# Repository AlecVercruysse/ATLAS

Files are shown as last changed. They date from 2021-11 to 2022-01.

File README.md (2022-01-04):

# ATLAS: Audio Tracking Laser-Assisted Light Show

Arya Goutam and Alec Vercruysse

---

This work, completed as a final project for E155 at Harvey Mudd College, takes in music input via a 3.5mm audio jack, and syncs
a diffraction-grating based laser light show to respond to percussive elements in the song. Read our [final report](papers/report.pdf) for a description of 
the design and algorithm.

Due to the requirements of the project for the class, all SystemVerilog code, including that for the FFT, was written from scratch.

 - `fpga/` contains the SystemVerilog code used to interface with the PCM1808 ADC, the FFT module, and the beat tracking algorithm. It also includes the python files used to generate the twiddle and hann windowing look up tables.
 - `mcu/` contains the code for the microcontroller, which was responsible for selecting patterns, driving the servo, and controlling the relays.
 - `adc/` contains the design files for the PCB developed to interface the ADC with the development platform we used for the class
 - `papers/` contains the initial project proposal and final report
 - `sim/` contains the jupyter notebooks used to prototype different parts of the design.

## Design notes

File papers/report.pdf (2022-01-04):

E155 MICROPROCESSORS. FINAL PROJECT. DECEMBER 2021 | 1

# ATLAS: Audio Tracking Laser-Assisted Light Show

## Arya Goutam and Alec Vercruysse

CONTENTS

I | Introduction | 1
I-A | Motivation | | 1
I-B | Overview | | 1
II | Design | 1
II-A | FPGA Design | | 1
II-A1 | ADC Interface | | 2
II-A2 | Fast | Fourier | Transform
Computation | | 3
II-A3 | Beat Onset Detection . . . . | 3
II-B | Microcontroller Design | | 4
III | Results | 5
Appendix A: Bill of Materials | 6
Appendix B: MAX10 FPGA SystemVerilog Code | 7
B-A | i2s.sv | | 7
B-B | fft.sv | | 12
B-C | spi.sv | | 18
B-D | beat_track.sv | | 21
B-E | testbenches.sv | | 23
B-F | twiddle.py | | 29
B-G | fft.cpp | | 30
Appendix C: STM32F401RE C Code | 33
C-A | Servo.c | | 33
References | 37

Abstract—We propose a design of a system that projects a laser light show that synchronizes to to music. The system samples audio input with a PCM1808 stereo ADC, and a MAX10 FPGA analyzes the frequency content of the song to find percussive elements in order to determine beat onsets. An STM32 microcontroller uses the beat onset locations to control a servo that rotates a multi-pattern diffraction grating and two laser diodes which shine through this grating. While in practice the design requires the song to have percussive elements and the algorithm is sensitive to input audio volume, the system can accurately identify and rapidly responds to beats and produces a compelling visual effect.

I. INTRODUCTION
A. Motivation

### Light shows are often used to enhance music but coordi-

nating lighting with music is challenging to do on the fly,

### especially with a low-cost setup. Our goal for this project

A. Goutam and A. Vercruysse are Engineering Majors in the class of 2023 at Harvey Mudd College, CA.

### was to design a system that automatically creates interesting

lighting effects which are synchronized to a live audio input.

B. Overview

### The system shown in Figure 1 above is described here:

1) Stereo audio is passed from a computer to the PCM.
2) The PCM passes digital audio output to the FPGA.

### 3) The FPGA reads the digital audio, computes beat onsets and sends pulses to the MCU when it detects a beat

onset.

### 4) The MCU uses the beat onset pulses to compute the song’s tempo, choose a light pattern according to the tempo, and synchronize the pattern with the beats of the

song.

### 5) The synchronized light pattern is displayed via control

signals to the lasers and the servo.

II. DESIGN

### The system consists of a straightforward signal path that

starts as the PCM1808 ADC samples the stereo audio input,

### and is then processed by the MAX10 FPGA. The FPGA then outputs beat onset information to the STM32 MCU, which

drives a hobby servo motor with diffraction grating attached.

A. FPGA Design

### The 10M08SAU169 FPGA is responsible for interfacing with the PCM1808 stereo audio ADC as well as performing the digital signal processing required to determine beat onsets from the audio signal. Beat detection is performed based on

the threshold detection of a spectral-based novelty function.

TABLE I
10M08SAU169 FPGA RESOURCE USAGE
Total Logic Elements | 6,060 / 8,064 | 75%
Total Pins | 26 / 130 | 20%
Total Memory Bits | 1,024 / 387,072 | < 1%
Total 9-bit multipliers | 12 / 48 | 25%

### This FPGA had just enough logic elements to implement all modules, including I2S, FFT, and beat detection. Table I demonstrates that 75% of logic elements are being used by the current design. However, since memory usage is extremely

small (corresponding to a single 32 bit x 32 sample RAM),

### Quartus is preferring to infer register logic rather than memory for some memory modules including twiddle bit ROM and

FFT RAM.

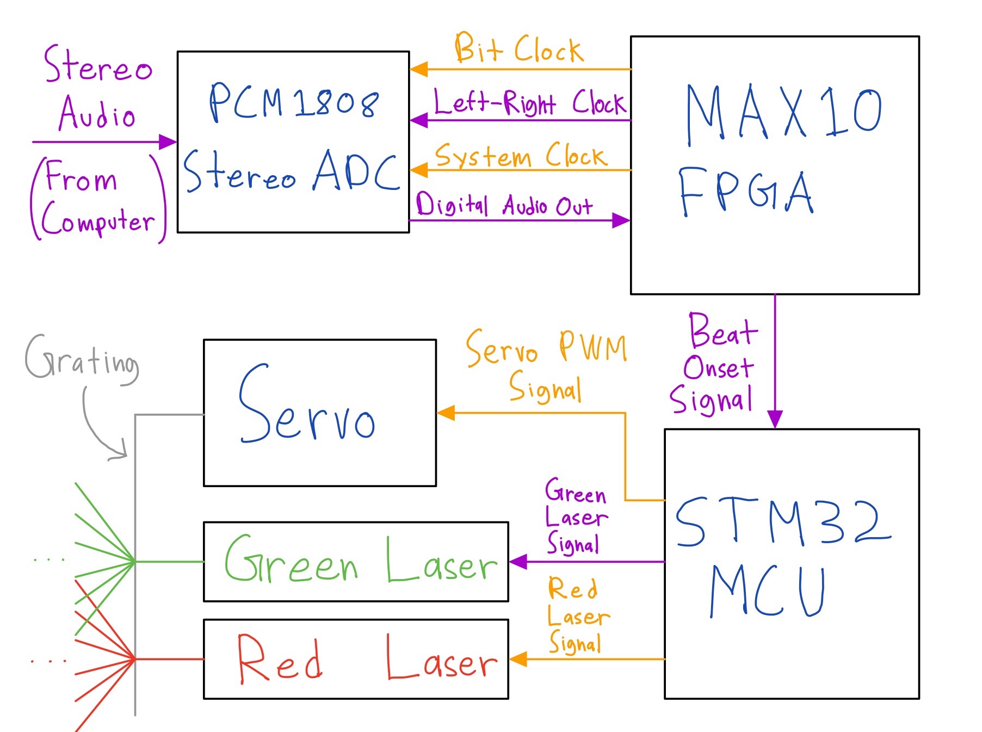
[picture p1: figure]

Fig. 1. System Block diagram displaying all components and signal paths within system.

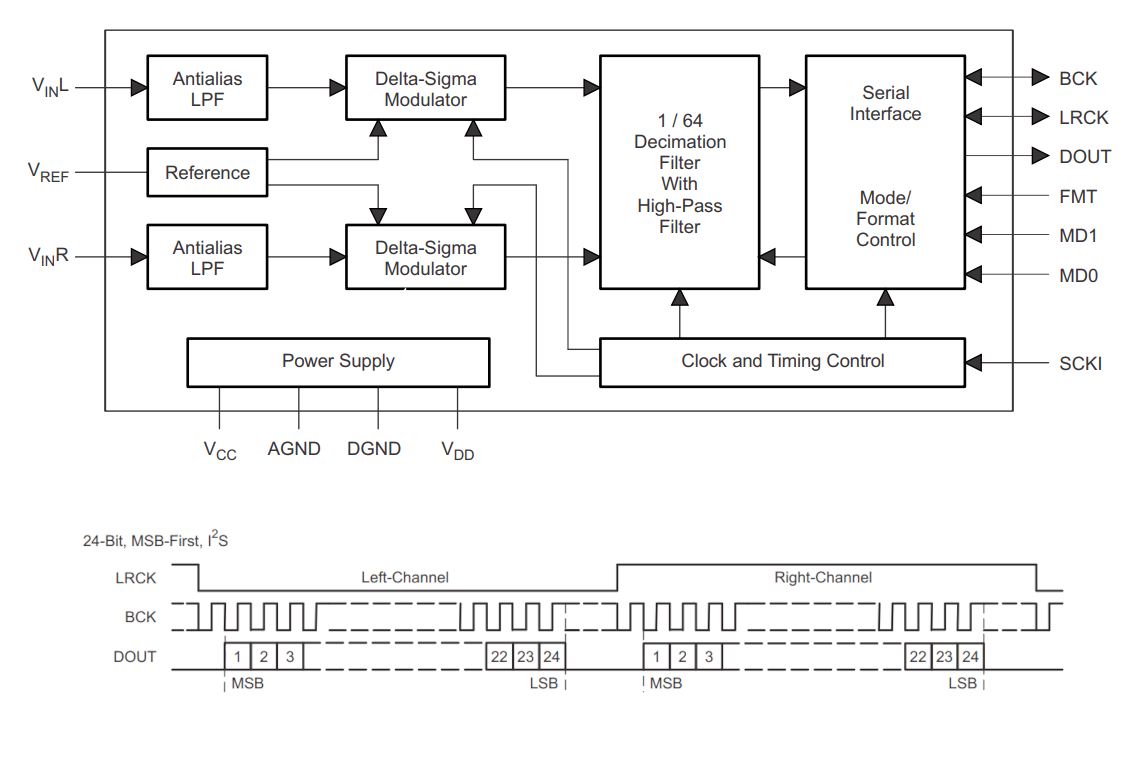
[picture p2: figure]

Fig. 2. Block diagram and relevant I2S communication protocol of the of the PCM1808 ADC used for audio input sampling. MD1=0, MD0=0, and FMT=0 to set the operating mode to slave-mode with I2S communication. AGND and DGND were tied together, with VCC and VDD tied to the 5V and 3.3V outputs of the Nucleo-64 development board, respectively.

### 1) ADC Interface: Although the FPGA includes an on-

board ADC, an external one was used to sample the audio.

### This was done in order to reduce the complexity of external hardware as well as provide for maximum possible flexibility

and minimum possible noise.

### Since conventional line-level audio signals are stereo, two

ADC channels are required in order to sample the song.

### Furthermore, line-level audio is zero centered, while the FPGA can only work with positive voltage, so therefore the signal would require biasing to sample with an FPGA. Lastly, the PCM1808 is much higher-performance than the FPGA – not only does it have 24 bit resolution (versus 12), it also

performs all required anti-aliasing filtering before sampling.

For a nominal 44.875 kHz sample rate, the PCM1808 samples at 3 MSPS and performs decimation and high pass to ensure that no aliasing occurs and no DC component exists in the signal. In addition, the PCM1808 exposes an extremely simple I2S slave-mode interface that allows for a fully synchronous design with the FPGA driving all sampling clocks, to allow for simple integration with the rest of the system. Lastly, the device requires only 3.3V and 5V power supplies, both of which already exist on the MAX10/Nucleo-64 development platform that is used for all work in E155. The block diagram

and I2S communication example waveform can be seen in Fig.

2.

Since the purpose of the E155 final project focused on digital logic design and no points were given for analog front end (AFE) design, the flexibility of the simple all-in-one solution of the PCM1808 was preferred to a more custom AFE that leveraged the existing ADC on-board the FPGA. The low component count required of this design also allowed for the extremely quick single-iteration development of a PCB for the PCM1808 and all associated audio jacks required to interface

the system with input audio.

A custom PCB was developed that included input (and output) 3.5mm and RCA audio jacks that allow the system to sit as a "man-in-the-middle" between an audio source and amplifier or listening device. The schematic of the PCB can be seen in Fig. 3. For maximum flexibility, all control signals were routed to the FPGA. Ultimately, the slave-mode I2S interface was selected, sampling at 46.875 kHz. This sampling frequency allows for a Nyquist frequency above 20 kHz, which

is considered to be the upper frequency limit of human hearing.

### Therefore this sampling frequency should accurately capture all audible information in the analog audio input. Since the

FPGA runs at 12MHz, the PCM1808 system clock (scki),

### which runs at 256∗46.875KHz = 12MHz was derived directly from the FPGA. Furthermore, a power of 2-based prescaler was used to derive the associated left/right clock (lrck) and

bit clock (bck) signals required for I2S communication.

### Since all I2S clock signals were derived from the same prescale counter, the value of the counter was also used to

determine state for the I2S master input module on the FPGA.

### For example, the bit index was determined by sampling the 5 bits (6:2) above the bit index sampled to derive the bit clock

(1).

### The bit index and left-right select clock were used to determine when to shift input data into the left and right channel shift registers. At the end of each frame consisting of a left and right channel sample, stable left/right sample registers were written to and an output "sample ready"

(newsample_valid) signal was generated.

### The operation of the I2S input module was verified via a

unit-testbench in ModelSim.
2) Fast Fourier Transform Computation: The 32-point Fast

Fourier Transform (FFT) is computed using a multi-cycle module based on the non-pipelined reference implementation by Slade in [1]. The design consists of a single butterfly unit which reads from and writes to two dual-port RAM blocks "ping-pong" configuration. That is, for a certain level of FFT computation, one RAM is reading pairs of a and b inputs to

the butterfly while the other is writing the resultant values. On the next level, the reading RAM becomes the writing one,

and the writing RAM becomes the reading one. An address generation unit (AGU) controls the logic to handle both the ping-pong operation of the RAM as well as determine the pairs of values that need to serve as inputs to the butterfly operation at each clock cycle. A block diagram of this implementation

is shown in Figure 4.

### Additional control logic was implemented in order to load the RAM with samples prior to computation, read the output

### spectrum values after computation, and reset the module after

computation.

### The state of the FPGA was determined by an external control Finite State Machine composed of the states

FFT_LOADING, FFT_STARTING, FFT_WAITING, FFT_WRITING and FFT_RESETTING. The state machine

waits in the FFT_LOADING state until 32 samples are loaded into the FFT, at which point it enters the FFT_STARTING state to drive the start logic. The state machine then enters the FFT_WAITING logic until it receives the done signal from the AGU. At this point the state machine enters the FFT_WRITING state to allow the output spectrum values to be read into another module. This control module also generates the addresses required to properly load and write out the data into and out of the FFT module. Once all values are written, the state machine enters FFT_RESETTING to reset the AGU before the next computation. After this, the

state goes back to FFT_LOADING and the cycle is repeated.

### The load logic was implemented by inferring multiplexers

between the AGU and RAM0 that allowed the write-enable,

### write-data, and address lines to be controlled by a load module that takes the input samples and writes them in the correct order to the FFT RAM 1

### The write logic was implemented in a similar manner, by inferring multiplexers that allowed the external FFT control module to access the address port of the RAM containing the

output values.

### The FFT computation is computed in less time than it takes to receive a single sample from the ADC, so all samples read in by the ADC are ultimately fed into the FFT module. This essentially results in an STFT module with a hop size equal

to the window size of 32.

The FFT module was verified with a unit-testbench in ModelSim, specifically by comparing output spectra to ones computed on identical input in Python with NumPy. Note that the output values reported in Table V of Slade do not match the values reported in Figure 3 of Slade, and are incorrect. Furthermore, our implementation uses roots-of-unity (twiddle) values wm = e

### −j2πm/N , while Slade uses a less standard convention, wm = e

### j2πm/N , which means that the sign of the imaginary parts of the output values produced

by the two different implementations of the FFT are flipped.

A crucial resource used when testing the FFT module was referencing a working C implementation (adapted from the one in Slade), which allowed ground-truth intermediate values to be examined. This was crucial to verifying the operation of the butterfly unit and address generation unit in particular. The

reference implementation is included in Appendix B-G.

### 3) Beat Onset Detection: The spectrum of a song can be considered to contain both harmonic and percussive information. Harmonic instruments and voices typically produce fundamental tones below 1 kHz, with harmonics of lower intensity appearing in frequency bins that are multiples of the

fundamental. Percussive elements, however, such as drums, can be considered to generate impulses in the time domain.

### Impulses in the time domain correspond to spectral content at

1with bit reversed addresses, see [1]

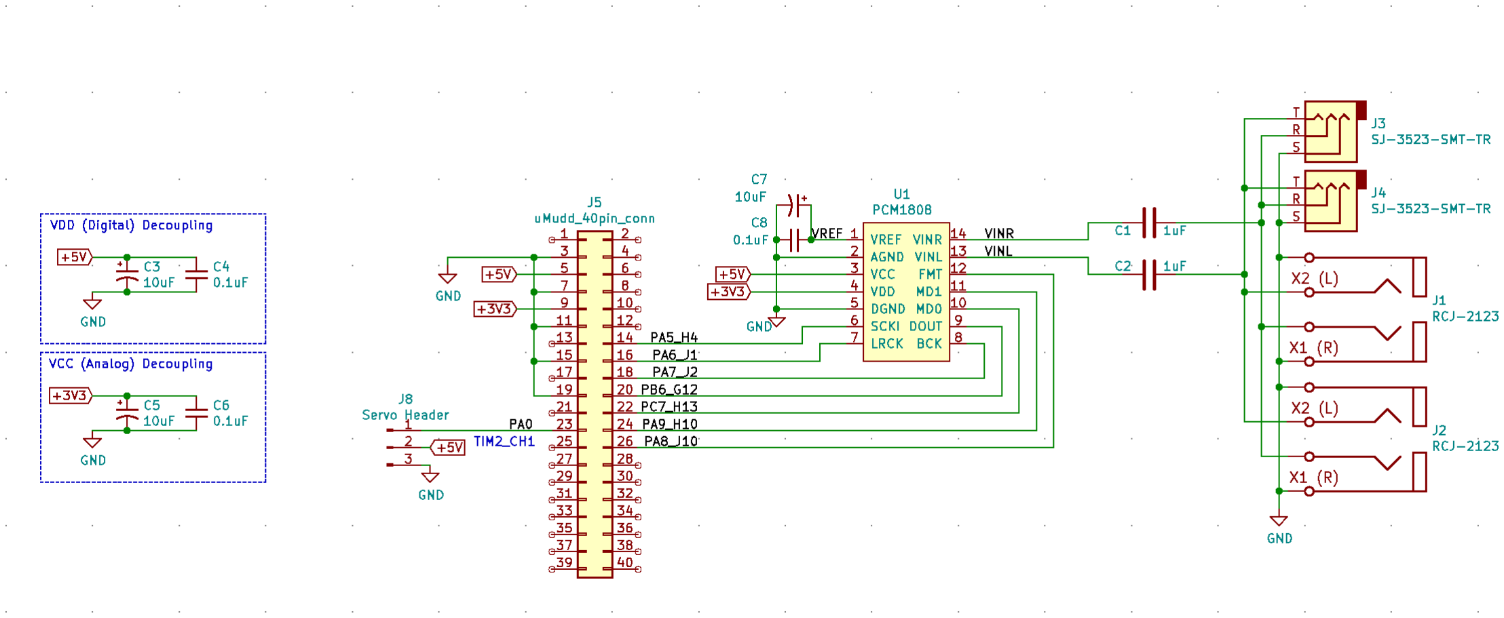
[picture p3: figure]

Fig. 3. Schematic of the ADC interface PCB. Note that the multiple audio jacks that allow it to be placed in the middle of an existing audio system.

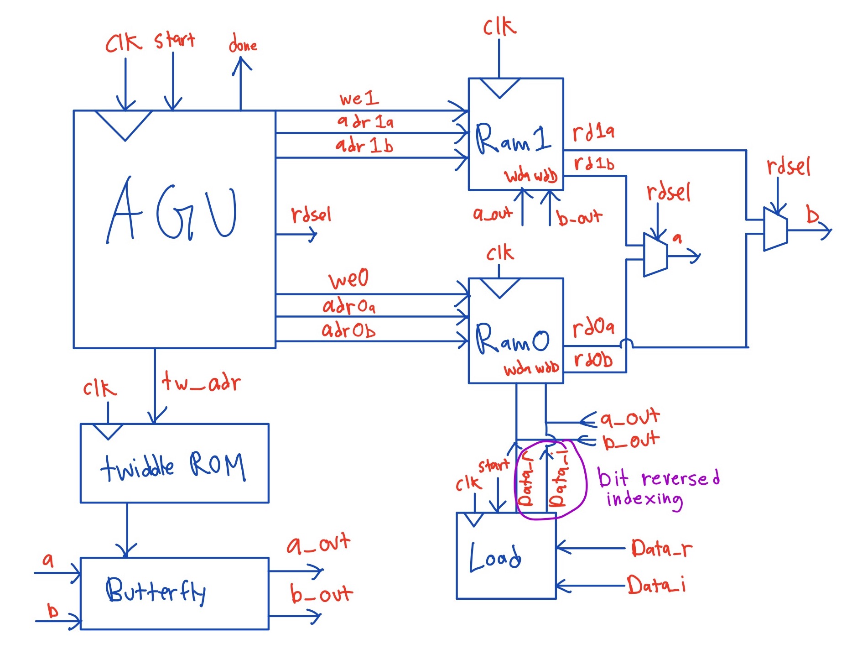
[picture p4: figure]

Fig. 4. Diagram of our Cooley-Tukey FFT System Verilog implementation based on Slade’s paper and Prof. Brake’s slides [1].

### every frequency, so often drums and percussive elements will appear in high-frequency bins, depending on the mastering of the song and the specific instruments involved. Figure 5 displays an example spectrum of an electronic dance music

(EDM) song that demonstrates this.

### To take advantage of the high-frequency and broadband nature of percussive components, beat onsets were calculated by performing debounced thresholding of a novelty function computed by summing the magnitudes of the upper frequency

bins.

As the output values of the FFT are being read sequen-tially, a complex multiplier computes the magnitude of each frequency bin by multiplying it with its complex conjugate. If the bin is between bins 10 and 15 inclusive, an accumulator accumulates this magnitude. The value of the accumulator is compared to a threshold to determine whether or not the sample could correspond to a beat. Hysteresis is implemented

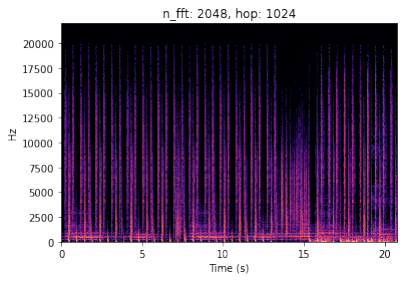
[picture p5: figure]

Fig. 5. Example log-magnitude Spectrum of a snippet of the EDM song "ACRAZE - Do it to It". Note that the upper frequency bins that correspond to the hi-hats provide steady tempo information, while the melodic and vocal parts of the song rest primarily in the lower frequency bins.

### to ensure that a single beat in the song that spans multiple

samples does not trigger the beat onset detector multiple times.

### Fig. 6 demonstrates this hysteresis for an example beat in a

song.

B. Microcontroller Design

### The STM32F401RE microcontroller (MCU) reads a pulsed beat onset signal from the FPGA and creates light patterns by

controlling the servo and the two lasers.

### The servo position is controlled by changing the duty cycle of a square wave signal. 770 µs of high time out of 20 ms corresponds to a position of zero degrees while 2270 µs corresponds to a position of 180 degrees. Positions are referred to as x µs. Our MCU simply writes out two binary signals for

laser control.
The lasers are controlled with a dual laser driver circuit.

### To create this circuit, we used a prebuilt dual laser driver

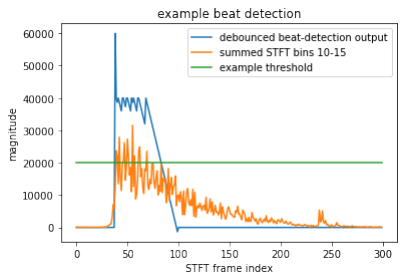
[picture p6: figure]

Fig. 6. Example beat-detection in the EDM song "ACRAZE - Do it to It". The orange trace corresponds to the sum of the upper frequency bins. The blue trace (beat detection out) goes high when the threshold is first reached. A "debounce" timer then counts down from there, resetting every time the threshold is reached, to only allow the beat to be detected again once the orange trace has been below the threshold for some minimum time. In practice, the blue signal only goes high when the beat is first detected, and the counter logic is stored and handled separately, but the logic displayed in this figure is helpful for visualization of the algorithm.

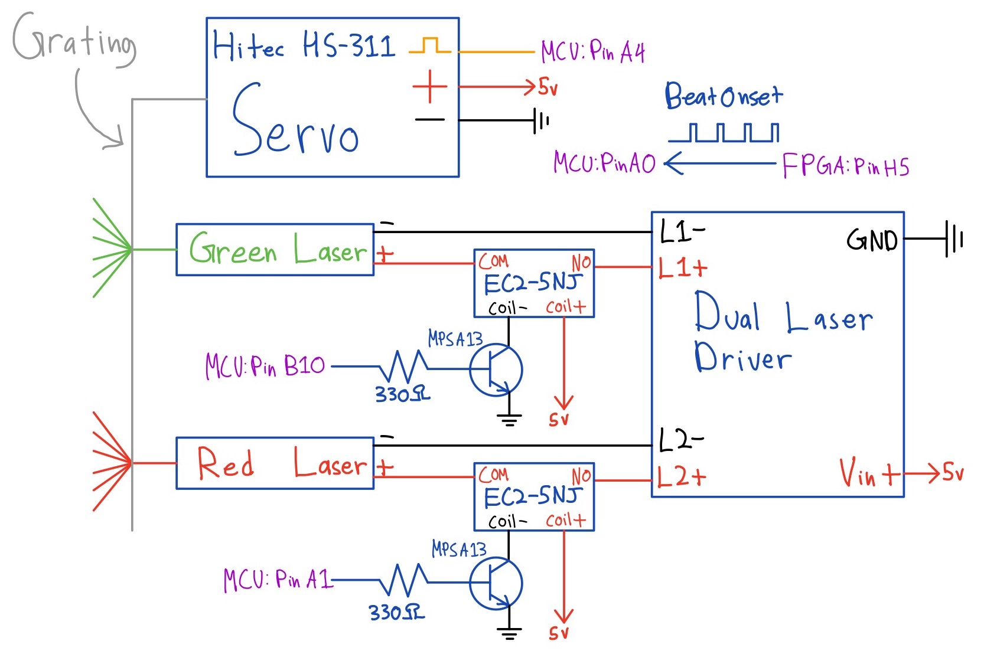
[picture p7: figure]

Fig. 7. Circuit diagram detailing physical connections between MCU, servo, and lasers.

board and inserted relays into the power wires going to the lasers. The MCU digital pins could not source enough current to activate the relays so we used NPN transistors to drive the relays and electrically control the flow of power to the lasers. We chose to use a relay instead of a transistor to avoid modifying the properties of the existing laser driver circuit. A circuit diagram of our MCU subsystem is presented in Figure

7.

A light pattern is encoded with four values: 1) Servo Starting Rotation (pulse width µs) 2) Servo Ending Rotation (pulse width µs) 3) Red Laser On (0 or 1) 4) Green Laser On (0 or 1) Beats per minute (BPM) is calculated using the time dif-ference between the last two beat onset pulses, and a pattern is assigned depending upon which bucket the BPM falls into from the following:

### - 0 < BPM ≤ 30 - 30 < BPM ≤ 60 - 60 < BPM ≤ 120 - 120 < BPM ≤ 240

### Once a pattern is selected, the servo oscillates between the servo start position and the servo end position. These transitions happen exactly at the beat onset times. The MCU also enables the lasers according to the selected pattern by writing the two binary "laser on" signals to our laser driver

circuit.

III. RESULTS

### The efficacy of our system is highly dependent upon the song that is fed into it. Songs with a consistent percussive

element, such as a clap or drum hit, produced the best results.

### In these cases, the beat onset detection algorithm captures nearly all of the beats and the lasers produce an aesthetically interesting light show that is closely synchronized to the input song. Additionally, the system functions best when the input

song is sent at maximum volume.

### There are a few ways we could have improved the system given more time: 1) Introduce an automatic gain control circuit. We believe this would allow for songs at varying volumes to perform

well with ATLAS.

### 2) Compute a log-magnitude spectrogram. Humans per-ceive the loudness of sound on a log scale so operating on a log-magnitude spectrogram is likely to yield beat detections that better align with a human’s perception of

beats.

### 3) Reduce the hop size of the STFT to be half of the window size by double-buffering the input sample win-dows, which provides for a more conventional STFT

computation.

4) Experiment with different FFT window sizes and bucket summation indices. Varying the window size and bucket summation indices could allow ATLAS to work on a greater variety of musical genres. For example, a higher FFT window size with beat detection based on a summation of the low frequency buckets could produce good

beat tracking in rock songs with a prominent bassline.

### Higher frequency resolution that enables the spectrum to differentiate fundamental frequencies of different notes would also enable the system to operate successfully with more conventional beat-detection algorithms such

as spectral-flux based novelty functions.

ACKNOWLEDGMENT

### The authors would like to thank Prof. Joshua Brake for his invaluable guidance with our final project. We also appreciate

the insightful feedback we received on our project by the class.

### Lastly, we thank Sam Abdelmuati in the stockroom for his help

regarding part selection.

APPENDIX A
BILL OF MATERIALS

TABLE II
BILL OF MATERIALS
Ct. | Description | Part Number | Extended Price
1 | stereo ADC | PCM1808PW | $2.23
2 | cap cer 1uf 50v 0805 | C2012JB1H105K085AB | $0.374
3 | cap cer 0.1uf 50v 0805 | CGA4J2X8R1H104K125AA | $0.396
3 | cap cer 10uf 25v 0805 | C2012JB1E106M085AC | $1.26
2 | conn jack stereo 3.5mm SMD | SJ-3523-SMT-TR | $1.88
1 | conn header vert 40pos 2.54mm | SBH11-PBPC-D20-ST-BK | $0.73
5 | JLCPCB boards (+ shipping) | – | $8.98
1 | laser + diffraction grating module (https://www.ebay.com/itm/-/254626113887?mkevt=1&mkcid=16&mkrid=711-127632-2357-0) | ZQ-B338 | $20.99
1 | Hitec hobby servo | HS-311 | N/A 2
2 | relay | EC2-5NJ | N/A 3
2 | NPN darlington transistor | MPSA13 | N/A 4
2 | 330 ohm resistor | – | N/A 5

2
already owned
3
from stock room
4
from stock room
5
from stock room

APPENDIX B
MAX10 FPGA SYSTEMVERILOG CODE
A. i2s.sv
1 | module final_fpga(input logic | clk, | // | 12MHz MAX1000 clk, H6
2 | input logic | nreset, // | global reset, | E6 (right btn)
3 | input logic | din, // | I2S DOUT, | PB6_G12
4 | input logic | uscki, // | SPI clk, | PB3_J12
5 | input logic | umosi, // | SPI MOSI, | PB5_J13
6 | input logic | uce, // | SPI CE, | PA10_L12
7 | input logic [3:0] | sw1, // | threshold sel. | E1, C2, C1, D1
,→ | (DIP SW1)
8 | output logic | bck, // | I2S bit clock, | PA7_J2
9 | output logic | lrck, // | I2S l/r clk, | PA6_J1
10 | output logic | scki, // | PCM1808 sys clk, | PA5_H4
11 | output logic | fmt, // | PCM1808 FMT, | PA8_J10
12 | output logic [1:0] md, // | PCM1808 MD1 & MD0, PC7_H13, PA9_H10
13 | output logic | miso, // | SPI MISO, | PB4_K11
14 | output logic [7:0] LEDs, // | debug LEDs | (see MAX1000 user
,→ | guide)
15 | output logic | beat_out // beat (to MCU) | H5 (thru a jumper
,→ | to MCU)
16 | );

17
18 | ///////////////////////////////// reset
19 | // active high reset, active low btns
20 | logic | reset;
21 | assign reset = ~(nreset);
22 | //assign LEDs[0] = reset;
23 | ///////////////////////////////// end reset

24
25 | ///////////////////////////////// I2S/PCM1808
26 | assign md | = 2'b00; // see PCM1808 table 2 (slave mode)
27 | assign fmt = 0; | // see PCM1808 table 3 (i2s mode)

28
29 | logic | newsample;
30 | logic [23:0] | left, right;
31 | i2s pcm_in(clk, reset, din, bck, lrck, scki, left, right, newsample);
32 | ///////////////////////////////// end I2S/PCM1808

33
34 | ///////////////////////////////// FFT
35 | logic | fft_start, fft_done, i2s_load, fft_load,
,→ | fft_reset, fft_creset, fft_write;
36 | logic [31:0] | fft_wd;
37 | logic signed [15:0] | left_msbs;
38 | logic signed [15:0] | fft_rd;
39 | logic [5:0] | sample_ctr;

40
41 | assign fft_reset = reset | fft_creset;
42 | assign left_msbs = left[23:8];
43 | assign fft_rd | = left_msbs >>> 5; // arithmetic shift right
44 | fft fft(clk, fft_reset, fft_start, fft_load, fft_rd, fft_wd, fft_done);
45 | fft_control i2s_fft_glue(clk, reset, newsample, fft_done, fft_start, fft_load,
,→ | fft_creset, fft_write, sample_ctr);
46 | ///////////////////////////////// end FFT

47
48 | ///////////////////////////////// store result
49 | logic [31:0] | res_count; // result count

50 | logic | posedge_fft_done;
51 | pos_edge pos_edge_fft_done(clk, fft_done, posedge_fft_done);
52 | always_ff @(posedge clk)
53 | begin
54 | if | (reset) | res_count <= 0;
55 | else if (posedge_fft_done) res_count <= res_count + 1'b1;
56 | end

57
58 | logic [31:0] | | spectrum_result [0:31];
59 | always_ff @(posedge clk) begin
60 | if (fft_write)
61 | begin
62 | spectrum_result[sample_ctr] <= fft_wd;
63 | end
64 | end
65 | ///////////////////////////////// end store result

66
67 | ///////////////////////////////// SPI
68 | logic [31:0] spi_data;
69 | logic [4:0] | spi_adr;
70 | assign spi_data = spectrum_result[spi_adr];
71 | spi_slave spi(clk, reset, uscki, umosi, uce, spi_data, spi_adr, miso);
72 | ///////////////////////////////// end SPI

73
74 | ///////////////////////////////// beat tracking
75 | logic [7:0] | thresh, accum_stable;
76 | logic | beat_ctr, posedge_beat_out;
77 | assign thresh = {1'b0, sw1, 2'b0};
78 | assign LEDs | = {accum_stable[7:1], beat_ctr};
79 | beat_track beattrack(clk, reset, sample_ctr, fft_wd, fft_write, fft_done, thresh,
,→ | beat_out, accum_stable);
80 | pos_edge pos_edge_beat_out(clk, beat_out, posedge_beat_out);

81
82 | always_ff @(posedge clk) begin
83 | if (reset)
84 | beat_ctr <= 0;
85 | else if (posedge_beat_out)
86 | beat_ctr <= beat_ctr + 1'b1;
87 | end
88 | ///////////////////////////////// end beat tracking

89
90 endmodule // final_fpga

91
92 | typedef enum logic [3:0] {FFT_LOADING, FFT_STARTING, FFT_WAITING, FFT_WRITING,
,→ | FFT_RESETTING, FFT_ERROR} statetype;
93 | module fft_control(input logic | clk,
94 | input logic | reset,
95 | input logic | newsample,
96 | input logic | fft_done,
97 | output logic | fft_start,
98 | output logic | fft_load,
99 | output logic | fft_reset,
100 | output logic | fft_write,
101 | output logic [5:0] sample_ctr);

102
103 | statetype | | state, nextstate;

104
105 | always_ff @(posedge clk) begin

106 | if | (reset || (state == FFT_RESETTING))
107 | sample_ctr <= 0;
108 | else if ((newsample && (state == FFT_LOADING)) || (state == FFT_WRITING ||
,→ | nextstate == FFT_WRITING))
109 | sample_ctr <= sample_ctr + 1'b1;
110 | else if (state == FFT_WAITING)
111 | sample_ctr <= 0; // this case needs to be checked after the previous
112 | // | in case state is WAITING but nextstate is WRITING.
113 | end

114
115 | always_ff @(posedge clk) begin
116 | if (reset) state <= FFT_LOADING;
117 | else state <= nextstate;
118 | end

119
120 | always_comb begin
121 | case (state)
122 | FFT_LOADING | :
123 | if (sample_ctr == 32) | nextstate = FFT_STARTING;
124 | else | nextstate = FFT_LOADING;
125 | FFT_STARTING : | nextstate = FFT_WAITING;
126 | FFT_WAITING | :
127 | if (fft_done) | nextstate = FFT_WRITING;
128 | else | nextstate = FFT_WAITING;
129 | FFT_WRITING | :
130 | if (sample_ctr == 32) | nextstate = FFT_RESETTING;
131 | else | nextstate = FFT_WRITING;
132 | FFT_RESETTING: | nextstate = FFT_LOADING;
133 | default | : | nextstate = FFT_ERROR; // debug
134 | endcase // case (state)
135 | end

136
137 | assign fft_load | = (state == FFT_LOADING) & newsample;
138 | assign fft_start = (state == FFT_STARTING);
139 | assign fft_reset = (state == FFT_RESETTING);
140 | assign fft_write = (state == FFT_WRITING || nextstate == FFT_WRITING);

141
142 endmodule // control

143
144 | module i2s(input logic | clk,
145 | input logic | reset,
146 | input logic | din, // | PCM1808 DOUT, | PB6_G12
147 | output logic | bck, // | bit clock, | PA7_J2
148 | output logic | lrck, // left/right clk, | PA6_J1
149 | output logic | scki, // PCM1808 system clock, PA5_H4
150 | output logic [23:0] left,
151 | output logic [23:0] right,
152 | output logic | newsample_valid);

153
154 | /////////////////// clock ////////////////////////////////////

155
156 | // | Fs = 46.875 KHz
157 | logic [8:0] | prescaler; // 9-bit prescaler
158 | assign scki = clk; | // 256 * Fs = 12 MHz
159 | assign bck | = prescaler[1]; // 64 | * Fs = 3 MHz = 12 MHz / 4
160 | assign lrck = prescaler[7]; // 1 | * Fs = 12 Mhz / 256

161
162 | always_ff @(posedge clk)

163 | begin
164 | if (reset)
165 | prescaler <= 0;
166 | else
167 | prescaler <= prescaler + 9'd1;
168 | end
169 | /////////////////// end clock ////////////////////////////////

170
171 | // left and right shift registers
172 | logic [23:0] | lsreg, rsreg;

173
174 | // samples the prescaler to figure out what bit should currently be sampled.
175 | // sampling occurs on bit 1 and bit 24, NOT bit 0!
176 | logic [4:0] | bit_state;
177 | assign bit_state = prescaler[6:2];

178
179 | // shift register enable logic
180 | logic | shift_en;
181 | assign shift_en = ((bit_state >= 1) && (bit_state <= 24) && !reset);

182
183 | // shift register operation. samples DOUT only when shift_en.
184 | // this should be the only register that is not clocked directly from clk!!
185 | always_ff @(posedge bck)
186 | begin
187 | if (!lrck && shift_en) | // left
188 | begin
189 | lsreg <= {lsreg[22:0], din};
190 | rsreg <= rsreg;
191 | end
192 | else if (lrck && shift_en) // right
193 | begin
194 | rsreg <= {rsreg[22:0], din};
195 | lsreg <= lsreg;
196 | end
197 | end // shift register operation

198
199 | // load shift regs into output regs.
200 | // update both regs at once, once every fs.
201 | // this way, left and right will always contain a valid sample.
202 | logic newsample;
203 | assign newsample = (bit_state == 25 && lrck && prescaler[1:0] == 0); // once every
,→ | cycle
204 | assign newsample_valid = (bit_state == 26 && lrck && prescaler[1:0] == 0); // once
,→ | we can sample it!
205 | always_ff @(posedge clk)
206 | begin
207 | if (reset)
208 | begin
209 | left <= 0;
210 | right <= 0;
211 | end
212 | else if (newsample)
213 | begin
214 | left <= lsreg;
215 | right <= rsreg;
216 | end
217 | else
218 | begin

219 | left <= left;
220 | right <= right;
221 | end
222 | end

223
224 endmodule // i2s

B. fft.sv
1 | // the width is the bit width (e.g. if width=16, 16 real and 16 im bits).
2 | // the input should be width-5 to account for bit growth.
3 | module fft
4 | #(parameter width=16, N_2=5, hann=0) // N_2 is log base 2 of N (points)
5 | (input logic | clk,
6 | input logic | reset,
7 | input logic | start,
8 | input logic | load,
9 | input logic [width-1:0] | rd, // real | read data in
10 | output logic [2*width-1:0] wd, // complex write data out
11 | output logic | done);

12
13 | logic | enable; | // for AGU operation
14 | logic | rdsel; | // read from RAM0 or RAM1
15 | logic | we0_agu, we0, we1; // RAMx write enable
16 | logic [N_2 - 1:0] | adr0a_agu, adr0b_agu, adr0a, adr0b, adr0a_load,
,→ | adr0b_load, adr0a_load_agu, adr1a, adr1b, adr1a_agu;
17 | logic [N_2 - 2:0] | twiddleadr; // twiddle ROM adr
18 | logic [2*width-1:0] | twiddle, a, b, writea, writeb, aout, bout, rd0a, rd0b,
,→ | rd1a, rd1b, val_in;

19
20 | // LOAD LOGIC
21 | fft_load #(width, N_2, hann) loader(clk, reset, load, rd, adr0a_load, adr0b_load,
,→ | val_in);
22 | assign adr0a_load_agu = load ? adr0a_load : adr0a_agu;
23 | assign adr0b = load ? adr0b_load : adr0b_agu;
24 | assign writea = load ? val_in : aout;
25 | assign writeb = load ? val_in : bout;
26 | assign we0 | = load ? | 1'b1 : we0_agu;

27
28 | // AGU ENABLE LOGIC
29 | always_ff @(posedge clk)
30 | begin
31 | if | (start) enable <= 1;
32 | else if (done || reset) | enable <= 0;
33 | end

34
35 | // OUTPUT LOGIC
36 | logic [N_2-1:0] out_idx;
37 | assign wd | = N_2[0] ? rd1a : rd1b; // ram holding results depends on even-ness of
,→ | log2(N-points)s?
38 | assign adr0a = done ? out_idx : adr0a_load_agu;
39 | assign adr1a = done ? out_idx : adr1a_agu;

40
41 | always_ff @(posedge clk)
42 | begin
43 | if | (reset) out_idx <= 0;
44 | else if (done) | out_idx <= out_idx + 1'b1;
45 | end

46
47 | fft_agu #(width, N_2) agu(clk, enable, reset, done, rdsel, we0_agu, adr0a_agu,
,→ | adr0b_agu, we1, adr1a_agu, adr1b, twiddleadr);
48 | fft_twiddleROM #(width, N_2) twiddlerom(twiddleadr, twiddle);

49
50 | twoport_RAM #(width, N_2) ram0(clk, we0, adr0a, adr0b, writea, writeb, rd0a, rd0b);
51 | twoport_RAM #(width, N_2) ram1(clk, we1, adr1a, adr1b, | aout, | bout, rd1a, rd1b);

52 | assign a = rdsel ? rd1a : rd0a;
53 | assign b = rdsel ? rd1b : rd0b;

54
55 | fft_butterfly #(width) bgu(twiddle, a, b, aout, bout);

56
57 endmodule // fft

58
59 | module fft_load
60 | #(parameter width=16, N_2=5, hann=0) // hann: bool, whether or not to window.
61 | (input logic clk,
62 | input logic | reset,
63 | input logic | load,
64 | input logic [width-1:0] | rd,
65 | output logic [N_2-1:0] | adr0a_load,
66 | output logic [N_2-1:0] | adr0b_load,
67 | output logic [2*width-1:0] val_in);

68
69 | logic [N_2-1:0] | idx;
70 | logic [width-1:0] | val_in_re;

71
72 | bit_reverse #(N_2) reverseaddr(idx, adr0a_load);
73 | assign adr0b_load = adr0a_load;

74
75 | always_ff @(posedge clk)
76 | begin
77 | if (reset) begin
78 | idx <= 0;
79 | end else if (load) begin
80 | idx <= idx + 1'b1;
81 | end
82 | end

83
84 | logic | [2*width-1:0] untruncated_mult;
85 | logic signed [width-1:0] | hann_coeff;
86 | hann_lut #(width, N_2) hann_rom(clk, idx, hann_coeff);
87 | assign untruncated_mult = hann_coeff * rd;
88 | assign val_in_re = hann ? untruncated_mult[2*width-2:width-1] : rd;
89 | assign val_in | = {val_in_re, 16'b0}; // imaginary is all zeros!

90
91 endmodule // fft_load

92
93 | module bit_reverse
94 | #(parameter N_2=5)
95 | (input logic [N_2-1:0] in,
96 | output logic [N_2-1:0] out);

97
98 | genvar | i;
99 | generate
100 | for(i=0; i<N_2; i=i+1) begin : BIT_REVERSE
101 | assign out[i] = in[N_2-i-1];
102 | end
103 | endgenerate

104
105 endmodule // bit_reverse

106
107 | // 32-point FFT address generation unit
108 | module fft_agu
109 | #(parameter width=16, N_2=5)

110 | (input logic | | clk,
111 | input logic | | enable,
112 | input logic | | reset,
113 | output logic | | done,
114 | output logic | | rdsel,
115 | output logic | | we0,
116 | output logic [N_2-1:0] adr0a,
117 | output logic [N_2-1:0] adr0b,
118 | output logic | | we1,
119 | output logic [N_2-1:0] adr1a,
120 | output logic [N_2-1:0] adr1b,
121 | output logic [N_2-2:0] twiddleadr);

122
123 | logic [N_2-1:0] | fftLevel = 0;
124 | logic [N_2-1:0] | flyInd = 0;

125
126 | logic [N_2-1:0] | adrA;
127 | logic [N_2-1:0] | adrB;

128
129 | always_ff @(posedge clk) begin
130 | if (reset) begin
131 | fftLevel <= 0;
132 | flyInd <= 0;
133 | end
134 | // Increment fftLevel and flyInd
135 | else if(enable === 1 & ~done) begin
136 | if(flyInd < 2**(N_2 - 1) - 1) begin
137 | flyInd <= flyInd + 1'd1;
138 | end else begin
139 | flyInd <= 0;
140 | fftLevel <= fftLevel + 1'd1;
141 | end
142 | end
143 | end

144
145 | // sets done when we are finished with the fft
146 | assign done = (fftLevel == (N_2));
147 | calcAddr #(width, N_2) adrCalc(fftLevel, flyInd, adrA, adrB, twiddleadr);

148
149 | assign adr0a = adrA;
150 | assign adr1a = adrA;

151
152 | assign adr0b = adrB;
153 | assign adr1b = adrB;

154
155 | // flips every cycle
156 | assign we0 = fftLevel[0] & enable;
157 | assign we1 = ~fftLevel[0] & enable;

158
159 | // flips every cycle
160 | assign rdsel = fftLevel[0];

161
162 endmodule // fft_agu

163
164 | // todo: parameterize for more than 32-point FFT.
165 | module calcAddr
166 | #(parameter width=16, N_2=5)
167 | (input logic | [N_2-1:0] | fftLevel,

168 | input logic [N_2-1:0] | flyInd,
169 | output logic [N_2-1:0] adrA,
170 | output logic [N_2-1:0] adrB,
171 | output logic [N_2-2:0] twiddleadr);

172
173 | logic [N_2-1:0] | tempA;
174 | logic [N_2-1:0] | tempB;

175
176 | always_comb begin
177 | tempA = flyInd << 1'd1;
178 | tempB = tempA + | 1'd1;
179 | adrA = ((tempA << fftLevel) | (tempA >> (N_2 - fftLevel))) & 5'h1f;

180
181 | adrB = ((tempB << fftLevel) | (tempB >> (N_2 - fftLevel))) & 5'h1f;
182 | twiddleadr = ((32'hffff_fff0 >> fftLevel) & 32'hf) & flyInd;
183 | end
184 | endmodule // calcAddr

185
186 | module fft_twiddleROM
187 | #(parameter width=16, N_2=5)
188 | (input logic | [N_2-2:0] twiddleadr, // 0 - 1023 = 10 bits
189 | output logic [2*width-1:0] twiddle);

190
191 | // twiddle table pseudocode: w[k] = w[k-1] * w,
192 | // where w[0] = 1 and w = exp(-j 2pi/N)
193 | // for k=0... N/2-1

194
195 | logic [2*width-1:0] | vectors [0:2**(N_2-1)-1];
196 | initial $readmemb("rom/twiddle.vectors", vectors);
197 | assign twiddle = vectors[twiddleadr];

198
199 endmodule // fft_twiddleROM

200

201
202 | // make sure the script rom/hann.py has been run with
203 | // the desired width! the `width` param should be equal to `q` in the script.
204 | // todo: test hann windowing (does the read need to be clocked)?
205 | module hann_lut
206 | #(parameter width=16, N_2=5)
207 | (input logic | clk,
208 | input logic [N_2-1:0] | idx,
209 | output logic [width-1:0] out);

210
211 | logic [width-1:0] | vectors[2**N_2-1:0];
212 | initial $readmemb("rom/hann.vectors", vectors);

213
214 | always @(posedge clk)
215 | out <= vectors[idx];

216
217 endmodule // hann_lut

218

219
220 | // explicit so that it is inferred, and we control
221 | // the truncation of the output.
222 | module mult
223 | #(parameter width=16)
224 | (input logic signed [width-1:0] | a,
225 | input logic signed [width-1:0] | b,

226 | output logic signed [width-1:0] out);

227
228 | logic [2*width-1:0] | untruncated_out;

229
230 | assign untruncated_out = a * b;
231 | assign out = untruncated_out[30:15];
232 | // see slade paper. this works as long as we're not
233 | // multiplying two maximum mag. negative numbers.

234
235 endmodule // mult

236

237
238 | module complex_mult
239 | #(parameter width=16)
240 | (input logic [2*width-1:0] | a,
241 | input logic [2*width-1:0] | b,
242 | output logic [2*width-1:0] out);

243
244 | logic signed [width-1:0] | a_re, a_im, b_re, b_im, out_re, out_im;
245 | assign a_re = a[31:16]; assign a_im = a[15:0];
246 | assign b_re = b[31:16]; assign b_im = b[15:0];

247
248 | logic signed [width-1:0] | a_re_be_re, a_im_b_im, a_re_b_im, a_im_b_re;
249 | mult #(width) m1 (a_re, b_re, a_re_be_re);
250 | mult #(width) m2 (a_im, b_im, a_im_b_im);
251 | mult #(width) m3 (a_re, b_im, a_re_b_im);
252 | mult #(width) m4 (a_im, b_re, a_im_b_re);

253
254 | assign out_re = (a_re_be_re) - (a_im_b_im);
255 | assign out_im = (a_re_b_im) + (a_im_b_re);
256 | assign out = {out_re, out_im};
257 | endmodule // complex_mult

258
259 | module fft_butterfly
260 | #(parameter width=16)
261 | (input logic [2*width-1:0] twiddle,
262 | input logic [2*width-1:0] | a,
263 | input logic [2*width-1:0] | b,
264 | output logic [2*width-1:0] aout,
265 | output logic [2*width-1:0] bout);

266
267 | logic signed [width-1:0] | a_re, a_im, aout_re, aout_im, bout_re, bout_im;
268 | logic signed [width-1:0] | b_re_mult, b_im_mult;
269 | logic [2*width-1:0] | b_mult;

270

271
272 | // expand to re and im components
273 | assign a_re = a[2*width-1:width];
274 | assign a_im = a[width-1:0];

275
276 | // perform computation
277 | complex_mult #(width) twiddle_mult(b, twiddle, b_mult);
278 | assign b_re_mult = b_mult[31:16];
279 | assign b_im_mult = b_mult[15:0];

280
281 | assign aout_re = a_re + b_re_mult;
282 | assign aout_im = a_im + b_im_mult;

283

284 | assign bout_re

= a_re

- b_re_mult;
285 | assign bout_im

= a_im

- b_im_mult;

286
287 | // pack re and im outputs
288 | assign aout | = {aout_re, aout_im};
289 | assign bout | = {bout_re, bout_im};

290
291 endmodule // fft_butterfly

292

293
294 | // adapted from HDL example 5.7 in Harris TB
295 | module twoport_RAM
296 | #(parameter width
=16, N_2

=

5

)

297 | (input logic | clk,
298 | input logic | we,
299 | input logic [N_2

1

:

0] | adra,
300 | input logic [N_2

1

:

0] | adrb,
301 | input logic

[

2

*width

1

:

0] | wda,
302 | input logic

[

2

*width

1

:

0] | wdb,
303 | output logic

[

2

*width

1

:

| | 0] rda,
304 | output logic

[

2

*width

1

:

| | 0] rdb);

305

306 | reg [
| 2 *width

1

:

0] | mem [

2**N_2

1

:

0];

307
308 | always @(posedge clk)
309 | if (we)
310 | begin
311 | mem[adra] <= wda;
312 | mem[adrb] <= wdb;
313 | end

314
315 | assign rda = mem[adra];
316 | assign rdb = mem[adrb];

317
318 endmodule // twoport_RAM

319
320 | module complex_mag
321 | #(parameter width
=16

)

322 | (input logic

[

2

*width

1

:

0] | a,
323 | output logic

[

2

*width

1

:

| | 0] out);

324
325 | logic [
| 2 *width

1

:

0] | b;
326 | logic signed [width

1

:

0] | b_re, b_im;

327
328 | assign b_re

= a[31

:16];
329 | assign b_im

=

-a[15

:

0];
330 | assign b = {b_re, b_im};

331
332 | complex_mult mag_mult(a, b, out);

333
334 endmodule // magnitude

C. spi.sv
1 | typedef enum logic [3:0] {SPI_IDLE, SPI_LOAD, SPI_WAIT, SPI_SHIFT, SPI_ERROR}
,→ | spi_state;
2 | module spi_slave(input logic | clk,
3 | input logic | reset,
4 | input logic | uscki, // non-synchronus miso
5 | input logic | umosi, // non-synchronus mosi
6 | input logic | uce, | // non-synchronus chip-enable
7 | input logic [31:0] data, | // 32-bit. based on adr.
8 | output logic [4:0] adr, | // to address data ram
9 | output logic | miso);

10
11 | // cpol = 0 (idle low)
12 | // cpha = 1 (shift on leading edge (posedge), sample on lagging edge (negedge)
13 | logic | | | scki, mosi, ce;
14 | sync scki_sync(clk, uscki, scki);
15 | sync mosi_sync(clk, umosi, mosi);
16 | sync | ce_sync(clk, | uce, | ce);

17
18 | logic | | | posedge_scki;
19 | pos_edge pos_edge_scki(clk, scki, posedge_scki);

20
21 | logic [31:0] | data_out;
22 | logic [4:0] | bit_idx;
23 | spi_state state, nextstate;

24
25 | assign miso = data_out[31]; // MSB. shifted out

26
27 | // SPI state register
28 | always_ff @(posedge clk) begin
29 | if (reset) state <= SPI_IDLE;
30 | else state <= nextstate;
31 | end

32
33 | // SPI state transition logic
34 | always_comb begin
35 | case (state)
36 | SPI_IDLE : if (ce) nextstate <= SPI_LOAD;
37 | else | nextstate <= SPI_IDLE;
38 | SPI_LOAD : nextstate <= SPI_WAIT;
39 | SPI_WAIT : if (posedge_scki) begin
40 | if (bit_idx != 31) nextstate <= SPI_SHIFT;
41 | else nextstate <= SPI_LOAD;
42 | | end
43 | else if (~ce) nextstate <= SPI_IDLE;
44 | else | nextstate <= SPI_WAIT;
45 | SPI_SHIFT : nextstate <= SPI_WAIT;
46 | default : nextstate <= SPI_ERROR;
47 | endcase // case (state)
48 | end

49
50 | // adr logic
51 | always_ff @(posedge clk) begin
52 | if (state == SPI_IDLE)
53 | | adr <= 0;
54 | else if (state == SPI_LOAD)
55 | adr <= adr + 1'b1;

56 | end

57
58 | // bit_idx logic
59 | always_ff @(posedge clk) begin
60 | if (state == SPI_IDLE || state == SPI_LOAD)
61 | bit_idx <=

0

;
62 | else if (state == SPI_SHIFT)
63 | bit_idx <= bit_idx

+ 1'b1

;
64 | end

65
66 | // data_out logic
67 | always_ff @(posedge clk) begin
68 | if (state == SPI_LOAD)
69 | data_out <= data;
70 | else if (state == SPI_SHIFT)
71 | data_out <= {data_out[30

:

0], 1'b0};
72 | end

73
74 endmodule // spi_slave

75
76 | // positive edge detection in synchronus logic
77 | module pos_edge(input logic clk,
78 | input logic | in,
79 | output logic out);

80
81 | logic | last;
82 | always_ff @(posedge clk) begin
83 | last <= in;
84 | end
85 | assign out

= (last ==

0 && in ==

1);

86
87 endmodule // pos_edge

88
89 | // negative edge detection in synchronus logic
90 | // (unused)
91 | module neg_edge(input logic clk,
92 | input logic | in,
93 | output logic out);

94
95 | logic | last;
96 | always_ff @(posedge clk) begin
97 | last <= in;
98 | end
99 | assign out

= (last ==

1 && in ==

0);

100
101 endmodule // pos_edge

102
103 | // synchronizer chain
104 | module sync(input logic clk,
105 | input logic | in,
106 | output logic out);

107
108 | logic | m1;
109 | always_ff @(posedge clk) begin
110 | m1 <= in;
111 | out <= m1;
112 | end

113

114 endmodule // sync

D. beat_track.sv
1 | typedef enum logic [1:0] {BEAT_LOAD, BEAT_EVAL, BEAT_RESET, BEAT_ERROR}
,→ | beat_load_state;
2 | module beat_track
3 | #(parameter wait_samples=30)
4 | (input logic | | clk,
5 | input logic | | reset,
6 | input logic [5:0] | sample_ctr,
7 | input logic [31:0] data,
8 | input logic | | fft_write,
9 | input logic | | fft_done,
10 | input logic [7:0] | thresh,
11 | output logic | | beat_out,
12 | output logic [7:0] debug);

13
14 | ///////////////////////////////// load control
15 | beat_load_state | | state, nextstate;
16 | always_ff @(posedge clk) begin
17 | if (reset) state <= BEAT_RESET;
18 | else | state <= nextstate;
19 | end

20
21 | always_comb
22 | case (state)
23 | BEAT_LOAD | :
24 | if (~fft_write) | nextstate = BEAT_EVAL;
25 | else | | nextstate = BEAT_LOAD;
26 | BEAT_EVAL | : | nextstate = BEAT_RESET;
27 | BEAT_RESET :
28 | if (fft_write) | nextstate = BEAT_LOAD;
29 | else | | nextstate = BEAT_RESET;
30 | BEAT_ERROR : | nextstate = BEAT_ERROR;
31 | default | : | nextstate = BEAT_ERROR;
32 | endcase // case (state)
33 | ///////////////////////////////// end load control

34
35 | ///////////////////////////////// accumulator
36 | logic [31:0] | | data_mag;
37 | logic signed [31:0] | accum, accum_stable;
38 | logic signed [15:0] | mag_real;

39
40 | assign debug = accum_stable[7:0];

41
42 | assign mag_real = data_mag[31:16];
43 | complex_mag magnitude(data, data_mag);

44
45 | // todo: potential error if we were to try to accumulate
46 | // | the first fft output sample (since we need
47 | // | the state to be out of BEAT_RESET to accum.)
48 | always_ff @(posedge clk) begin
49 | if (reset || (state == BEAT_RESET))
50 | begin
51 | accum <= 0;
52 | // accum_stable <= 0; // debug, easier not to reset
53 | end
54 | // choose bins 10..16 (see sim .ipynb)
55 | else if ((sample_ctr >= 10) && (sample_ctr <= 16) && fft_write)

56 | begin
57 | accum <= accum + mag_real;
58 | end
59 | if (state == BEAT_EVAL)
60 | accum_stable <= accum;
61 | end
62 | ///////////////////////////////// end accumulator

63
64 | ///////////////////////////////// beat filter
65 | logic [31:0] | wait_ctr;
66 | logic | over;

67
68 | // debouncing & thresholding logic
69 | always_ff @(posedge clk) begin
70 | if (reset) begin
71 | wait_ctr <= wait_samples + 1'b1;
72 | over <= 0;
73 | end
74 | else if (state == BEAT_EVAL) begin
75 | if (accum > thresh) begin // threshold met
76 | wait_ctr <= 0;
77 | over <= 1;
78 | end else begin | // threshold not met
79 | if (wait_ctr > wait_samples) begin
80 | over <= 0;
81 | wait_ctr <= wait_ctr;
82 | end else begin
83 | wait_ctr <= wait_ctr + 1'b1;
84 | over <= over;
85 | end
86 | end
87 | end // if (state == BEAT_EVAL)
88 | end // always_ff @ (posedge clk)

89
90 | always_ff @(posedge clk) begin
91 | if (state == BEAT_EVAL) begin
92 | if ((accum > thresh) && ~over && (wait_ctr > wait_samples))
93 | beat_out <= 1;
94 | else
95 | beat_out <= 0;
96 | end
97 | end
98 | ///////////////////////////////// end beat filter

99

100
101 endmodule // beat_track

E. testbenches.sv

module i2s_testbench();
logic clk, reset, din, bck, lrck, scki; logic [24:0] left, right; // 23 + 1 msb pad
4 | logic [8:0] | i;
| initial
forever begin
clk = 1'b0; #5;
clk = 1'b1; #5;
| end

initial begin
reset = 1'b1;
| i = 0;
| end

i2s dut(clk, reset, din, bck, lrck, scki, left, right);

always @(posedge clk) begin
if (i == 10)
reset = 0;
| i = i + 1;
| end
endmodule // i2s_testbench

// requires manually checking! compare to values in file.
// need to copy the rom/ dir into the simulation/modelsim/ dir module hannrom_testbench #(parameter width=16, N_2=5)(); logic clk;
logic [N_2-1:0] idx;
logic [width-1:0] out;

// clk. if ns scale, then we're running @ 11.9 MHz initial
forever begin
clk = 1'b0; #5;
clk = 1'b1; #5;
end

initial begin
idx = 0;
end

always @(posedge clk) begin idx =idx+1'b1;
end

hann_lut dut(clk, idx, out);

endmodule // twiddlerom_testbench

// tested
module bgu_testbench #(parameter width=16)(); logic clk;
logic [2*width-1:0] twiddle;

57 | logic [2*width-1:0] a;
58 | logic [2*width-1:0] b;
59 | logic [2*width-1:0] aout;
60 | logic [2*width-1:0] bout;

61
62 | initial
63 | forever begin
64 | clk = 1'b0; #5;
65 | clk = 1'b1; #5;
66 | end

67
68 | initial begin
69 | twiddle = 0;
70 | a = 0;
71 | b = 0;
72 | aout = 0;
73 | bout = 0; #10;
74 | assert (aout===0 && bout===0) else $error("case 1 failed.");

75
76 | twiddle = {16'h7FFF, 16'b0}; #10; assert(aout===0 && bout===0) else $error("case
,→ | 2 failed.");
77 | b = {16'h7FFF, 16'b0}; #10; assert(aout==={16'h7FFE,16'b0} && bout==={16'h8002,
,→ | 16'b0}) else $error("case 3 failed.");

78
79 | // real test case:
80 | // real b*w out: 0xEE59 (-4520). im b*w out: 0x58C2 (22722).
81 | // aout: 141 + j27382. bout: | 9179 - j18062.
82 | twiddle = {16'h471C, 16'h6A6C}; a={16'h1234, 16'h1234}; b={16'h3FFF, 16'h3FFF};
,→ | #10;
83 | assert(aout==={16'h008C, 16'h6AF6} && bout==={16'h23DC, 16'hB972}) else
,→ | $error("case 4 failed!");

84
85 | $display("BGU tests complete.");
86 | end

87
88 | fft_butterfly dut(twiddle, a, b, aout, bout);

89
90 endmodule // twiddlerom_testbench

91
92 | // verify that RAM works, and is fully two-port.
93 | // tested.
94 | module ram_testbench #(parameter width=16, N_2=5)();
95 | logic clk;
96 | initial
97 | forever begin
98 | clk = 1'b0; #5;
99 | clk = 1'b1; #5;
100 | end

101
102 | logic | we;
103 | logic [N_2-1:0] | adra;
104 | logic [N_2-1:0] | adrb;
105 | logic [2*width-1:0] wda;
106 | logic [2*width-1:0] wdb;
107 | logic [2*width-1:0] rda;
108 | logic [2*width-1:0] rdb;

109
110 | twoport_RAM #(width, N_2) dut(clk, we, adra, adrb, wda, wdb, rda, rdb);

111
112 | initial begin
113 | we = 0; adra = 0; adrb = 0; wda = 0; wdb = 0; rda = 0; rdb = 0; #10
114 | adra = 10; adrb = 12; wda = 10; wdb = 12; we = 1; #10;
115 | we = 0; #20; adra = 12; adrb = 10; #10; assert(rda === 12 && rdb === 10) else
,→ | $error("ram test failed.");
116 | end

117
118 endmodule // ram_testbench

119

120
121 | // outdated (reset signal). previously tested working.
122 | module agu_testbench #(parameter width=16, N_2=5)();

123
124 | // inputs
125 | logic clk;
126 | initial
127 | forever begin
128 | clk = 1'b0; #5;
129 | clk = 1'b1; #5;
130 | end
131 | logic | start;

132
133 | // outputs
134 | logic | done;
135 | logic | rdsel;
136 | logic | we0;
137 | logic [N_2-1:0] adr0a;
138 | logic [N_2-1:0] adr0b;
139 | logic | we1;
140 | logic [N_2-1:0] adr1a;
141 | logic [N_2-1:0] adr1b;
142 | logic [N_2-2:0] twiddleadr;

143
144 | fft_agu #(width, N_2) agu(clk, start, done, rdsel, we0, adr0a, adr0b, we1, adr1a,
,→ | adr1b, twiddleadr);

145
146 | initial begin
147 | // init inputs and outputs to zero/default
148 | start = 0; done = 0; rdsel = 0; we0 = 0; adr0a = 0; adr0b = 0; we1 = 0; adr1a =
,→ | 0; adr1b = 0; twiddleadr = 0; #10;

149
150 | // init inputs to starting values.
151 | start = 1; #10;
152 | end

153
154 endmodule // agu_testbench

155
156 | // fft module test.
157 | // loads input from | rom/slade_test_in.memh,
158 | // compares output to | rom/slade_test_out.memh,
159 | // writes computed output to rom/fft_test_out.memh.
160 | // (see "/sim/verify sim fft.ipynb" to process output)
161 | //
162 | // Note that the slade output values are incorrect, so we should
163 | // verify in the jupyter notebook, not with slade_test_out.memh
164 | module slade_fft_testbench();
165 | logic clk;

166 | logic start, load, done, reset;
167 | logic signed [15:0] rd, expected_re, expected_im, wd_re, wd_im;
168 | logic [31:0] | wd;
169 | logic [31:0] | idx, out_idx, expected;

170
171 | logic [15:0] | input_data [0:31];
172 | logic [31:0] | expected_out [0:31];

173

174 | //
,→ | https://stackoverflow.com/questions/25607124/test-bench-for-writing-verilog-output-to-a-text-file
175 | integer | f; // file pointer?

176
177 | fft #(16, 5, 0) dut(clk, reset, start, load, rd, wd, done); // no hann

178

179 | // clk
180 | always
181 | begin
182 | clk = 1; #5; clk=0; #5;
183 | end

184
185 | // start of test
186 | initial
187 | begin
188 | $readmemh("rom/slade_test_in.memh", input_data);
189 | $readmemh("rom/slade_test_out.memh", expected_out);
190 | f = $fopen("rom/fft_test_out.memh", "w"); // write computed vals
191 | idx=0; reset=1; #40; reset=0;
192 | end

193
194 | always @(posedge clk)
195 | if (~reset) idx <= idx + 1;
196 | else idx <= idx;

197
198 | always @(posedge clk)
199 | if (load) out_idx <= 0;
200 | else if (done) out_idx <= out_idx + 1;

201
202 | // load/start logic
203 | assign load = | idx < 32;
204 | assign start = idx === 32;
205 | assign rd = load ? input_data[idx[4:0]] : 0;
206 | assign expected = expected_out[out_idx[4:0]];
207 | assign expected_re = expected[31:16];
208 | assign expected_im = expected[15:0];
209 | assign wd_re = wd[31:16];
210 | assign wd_im = wd[15:0];

211
212 | always @(posedge clk)
213 | if (done) begin
214 | if (out_idx <= 31) begin
215 | $fwrite(f, "%h\n", wd);
216 | if (wd !== expected) begin
217 | $display("Error @ out_idx %d: expected %b (got %b) | expected: %d+j%d,
got %d+j%d", out_idx, expected, wd, expected_re, expected_im, wd_re, wd_im);

,→

,→

218 | end
219 | end else begin
220 | $display("Slade FFT test complete.");

$fclose(f);

end

end
endmodule // fft_testbench

module toplevel_testbench();
logic clk, nreset, din, uscki, umosi, miso, bck, lrck, scki, fmt, uce, beat_out; logic [7:0] LEDs;
logic [1:0] md;

logic [63:0] idx;
logic [31:0] sample_idx, bck_idx; logic [24:0] input_sample;
logic [23:0] input_data [0:9720234];

// clk
always
begin
clk = 1; #5; clk=0; #5;

end

always_ff @(posedge clk)
if (~nreset) idx <= idx + 1; else idx <= idx;

initial begin
$readmemh("rom/toplevel_test_in.memh", input_data); sample_idx = 0;
nreset = 0; #100; nreset = 1;

end

// feed in samples!
always @(negedge lrck) begin
input_sample <= {1'b0, input_data[sample_idx]}; sample_idx <= sample_idx + 1;

end
always @(negedge bck) begin
input_sample <= {input_sample[23:0], 1'b0}; // 25 bits wide to account for first ,→ non-sampling bck.

end
assign din = lrck ? 0 : input_sample[24];

final_fpga dut(clk, nreset, din, uscki, umosi, uce, bck, lrck, scki, fmt, md, miso, ,→ LEDs, beat_out);

// spi stuff
always begin
uscki = 1; #30; uscki = 0; #30;

end

initial begin
umosi = 0;
uce=0;
#200000;

uce=1;

end endmodule // toplevel_testbench

module spi_testbench();
logic clk, reset;
logic uscki, umosi, miso, uce; logic [31:0] data;
283 | logic [4:0] | adr;
logic [31:0] sreg_in;

assign data = {27'b0, adr}; // simple

// clk
always
begin
clk = 1; #5; clk=0; #5;

end

always begin
uscki = 1; #30; uscki = 0; sreg_in = {sreg_in[30:0], miso}; #30;

end

initial begin
umosi = 0; uce = 0; reset=1; #100; reset=0; #100; uce=1;

end

spi_slave dut(clk, reset, uscki, umosi, uce, data, adr, miso);

endmodule // spi_testbench

F. twiddle.py

# Alec Vercruysse

# 2021-11-16

# generate N-point q-bit two's complement integer twiddle bits

import numpy as np

# required since we need signed represntation

# https://stackoverflow.com/questions/699866/python-int-to-binary-string

def int2bin(integer, digits):
if integer >= 0:
return bin(integer)[2:].zfill(digits) else:
return bin(2**digits + integer)[2:]

i2b = np.vectorize(int2bin)

N = 32
q = 16

n = np.arange(N/2)
#wi = np.exp(1j * np.pi*2/N) #w = np.power(wi, n)

#w_re = np.real(w)

w_re = np.cos(2*np.pi*n/N)
w_re = (w_re * (2**(q-1) - 1)).astype('int') w_re = i2b(w_re, q)

# w_im = np.imag(w)

w_im = -np.sin(2*np.pi*n/N)
w_im = (w_im * (2**(q-1) - 1)).astype('int') w_im = i2b(w_im, q)

with open("twiddle.vectors", 'w') as f: for i in range(len(w_re)):
f.write(w_re[i] + "" + w_im[i] + "\n")

with open("../simulation/modelsim/rom/twiddle.vectors", 'w') as f: for i in range(len(w_re)):
f.write(w_re[i] + "" + w_im[i] + "\n")

G. fft.cpp

Used to verify the FPGA FFT operation.

1 //32 point FFT implementation in C++ based on Slade paper

2
3 #include <stdio.h>

4
5 int main(){

6
7 | typedef int16_t newType;

8
9 | // Initial real data
10 | newType Data_r[32] = {
11 | 0x3FF,
12 | 0x3FF,
13 | 0xfc01,
14 | 0xfc01,

15
16 | 0x3FF,
17 | 0x3FF,
18 | 0xfc01,
19 | 0xfc01,

20
21 | 0x3FF,
22 | 0x3FF,
23 | 0xfc01,
24 | 0xfc01,

25
26 | 0x3FF,
27 | 0x3FF,
28 | 0xfc01,
29 | 0xfc01,

30
31 | 0x3FF,
32 | 0x3FF,
33 | 0xfc01,
34 | 0xfc01,

35
36 | 0x3FF,
37 | 0x3FF,
38 | 0xfc01,
39 | 0xfc01,

40
41 | 0x3FF,
42 | 0x3FF,
43 | 0xfc01,
44 | 0xfc01,

45
46 | 0x3FF,
47 | 0x3FF,
48 | 0xfc01,
49 | 0xfc01
50 | };

51
52 | // Initial imaginary data
53 | newType Data_i[32] = {
54 | 0x0,
55 | 0x0,

56 | 0x0 ,
57 | 0x0 ,
58 | 0x0 ,
59 | 0x0 ,
60 | 0x0 ,
61 | 0x0 ,
62 | 0x0 ,
63 | 0x0 ,
64 | 0x0 ,
65 | 0x0 ,
66 | 0x0 ,
67 | 0x0 ,
68 | 0x0 ,
69 | 0x0 ,
70 | 0x0 ,
71 | 0x0 ,
72 | 0x0 ,
73 | 0x0 ,
74 | 0x0 ,
75 | 0x0 ,
76 | 0x0 ,
77 | 0x0 ,
78 | 0x0 ,
79 | 0x0 ,
80 | 0x0 ,
81 | 0x0 ,
82 | 0x0 ,
83 | 0x0 ,
84 | 0x0 ,
85 | 0x0
86 | };

87
88 | // twiddle factors real
89 | newType Tw_r[16 ] = {
90 | 0x7fff ,
91 | 0x7d89 ,
92 | 0x7641 ,
93 | 0x6a6d ,
94 | 0x5a82 ,
95 | 0x471c ,
96 | 0x30fb ,
97 | 0x18f9 ,
98 | 0x0 ,
99 | 0xe707 ,
100 | 0xcf05 ,
101 | 0xb8e4 ,
102 | 0xa57e ,
103 | 0x9593 ,
104 | 0x89bf ,
105 | 0x8277
106 | };

107
108 | // twiddle factors imaginary
109 | newType Tw_i[16 ] = {
110 | 0 ,
111 | 0x1859 ,
112 | 0x30fb ,
113 | 0x471c ,

0x5a82,
0x6a6d,
0x7641,
0x7d89,
0x7fff,
0x7d89,
0x7641,
0x6a6d,
0x5a82,
0x471c,
0x30fb,
0x1859

};

for(newType i = 0; i < 5; i++){ // 5 levels for 2^5 = 32 point FFT for(newType j = 0; j < 16; j++){ // operating on 16 bit ints
newType ja=j<<1;
newType jb=ja+1;
ja = ((ja << i) | (ja >> (5-i))) & 0x1f; // Address A; 5 bit circular left
,→ shift
jb = ((jb << i) | (jb >> (5-i))) & 0x1f ; // Address B; implemented using
,→ C statements
newType TwAddr = ((0xfffffff0 >> i) & 0xf) & j; // Twiddle addresses

newType temp_r = ((Data_r[jb] * Tw_r[TwAddr]) / 32768) - ((Data_i[jb] * ,→ Tw_i[TwAddr]) /32768);
newType temp_i = ((Data_r[jb] * Tw_i[TwAddr]) / 32768) + ((Data_i[jb] * ,→ Tw_r[TwAddr]) / 32768);
if(ja == 0 || jb == 0){
| printf("2nd val, ja: %d, jb: %d, realA: %x, realB %x, tempR: %x, tempI: %x, TwR: %x, TwI: %x, TwAddr: %d, \n",ja, jb, Data_r[ja],
| Data_r[jb],temp_r, temp_i, Tw_r[TwAddr], Tw_i[TwAddr], TwAddr);

,→

,→

}

//Sets data for level
Data_r[jb] = Data_r[ja] - temp_r; Data_i[jb] = Data_i[ja] - temp_i; Data_r[ja] += temp_r;
Data_i[ja] += temp_i;

}
for(newType k = 0; k < 32; k++){
printf("%d %x %x \n", k, Data_r[k], Data_i[k]);

}

}

}

APPENDIX C

### STM32F401RE C CODE

Requires standard E155 libraries provided by Prof. Brake.

A. Servo.c
1 | #include <stdio.h>
2 | #include "STM32F401RE.h"

3
4 | ////////////////////////////////////////////////
5 | // Constants
6 | ////////////////////////////////////////////////

7
8 | #define SERVO_PIN | 4 // GPIOA
9 | #define BEAT_PIN | 0 // GPIOA
10 | #define GREEN_PIN | 10 // GPIOB
11 | #define RED_PIN | 1 // GPIOA

12
13 #define USART_ID USART2_ID

14
15 | #define MIN_MICROS 770
16 | #define MAX_MICROS 2270
17 | #define CYCLE_MICROS 20000

18
19 | // Used for testing
20 | const float usPerDeg = (MAX_MICROS - MIN_MICROS)/180;
21 | // takes in an angle from 0-180, spits out microseconds to write to servo
22 | long angleToMicros(float angle){
23 | return (long)(angle * usPerDeg) + MIN_MICROS;
24 | }

25
26 // Servo Pattern points

27
28 | // Red laser pattern locations
29 | #define RPP0 770
30 | #define RPP1 917
31 | #define RPP2 1022
32 | #define RPP3 1136
33 | #define RPP4 1242
34 | #define RPP5 1370
35 | #define RPP6 1465
36 | #define RPP7 1599
37 | #define RPP8 1724
38 | #define RPP9 1852
39 | #define RPPA 1960
40 | #define RPPB 2084
41 | #define RPPC 2204
42 | #define RPPD 2269

43
44 | // Green laser pattern locations
45 | #define GPP0 770
46 | #define GPP1 870
47 | #define GPP2 966
48 | #define GPP3 1091
49 | #define GPP4 1208
50 | #define GPP5 1328
51 | #define GPP6 1442
52 | #define GPP7 1532

53 | #define GPP8 1664
54 | #define GPP9 1792
55 | #define GPPA 1862
56 | #define GPPB 1978
57 | #define GPPC 2134
58 | #define GPPD 2269

59
60 //Pattern set 1

61
62 | // start, end, red, green
63 | // | int pats[6][4] = {
64 | // | {GPP0, | GPP1, 1, 1},
65 | // | {RPP0, | RPP1, 0, 1},
66 | // | {GPP2, GPP3, | 1, 1},
67 | // | {RPP3, RPP4, | 1, 0},
68 | // | {RPP5, RPP6, | 1, 0},
69 | // | {RPP7, RPP8, | 1, 0} //1328, 1442
70 | // | };

71
72 // Pattern set 2

73
74 | int pats[6][4] = {
75 | {GPPC, | GPPD, 1, 1},
76 | {GPPA, | GPPB, 1, 1},
77 | {GPP8, GPP9, | 0, 1},
78 | {RPP6, RPP7, | 1, 0},
79 | {RPP4, RPP5, | 1, 0},
80 | {RPP2, RPP3, | 1, 0}
81 | };

82
83 | // used for printing
84 | char text[50];

85
86 | int main(void) {
87 | // Configure flash latency and set clock to run at 84 MHz
88 | configureFlash();

89
90 | /* Configure APB prescalers
91 | 1. Set APB2 (high-speed bus) prescaler to no division
92 | 2. Set APB1 (low-speed bus) to divide by 2.
93 | */
94 | RCC->CFGR.PPRE2 = 0b000;
95 | RCC->CFGR.PPRE1 = 0b100;

96
97 | configureClock();

98
99 | // Enable GPIOA clock
100 | RCC->APB2ENR |= (1 << 16); //Enable TIM10
101 | RCC->APB2ENR |= (1 << 17); //Enable TIM10
102 | RCC->APB2ENR |= (1 << 18); //Enable TIM11
103 | RCC->AHB1ENR.GPIOAEN = 1; // Enable GPIOA Clock
104 | RCC->AHB1ENR.GPIOBEN = 1; // Enable GPIOA Clock

105
106 | // Servo Pin
107 | pinMode(GPIOA, SERVO_PIN, GPIO_OUTPUT);
108 | // Beat Pin from FPGA
109 | pinMode(GPIOA, BEAT_PIN, GPIO_INPUT);
110 | // Red Laser Transistor -> Relay

111 | pinMode(GPIOA, RED_PIN, GPIO_OUTPUT);
112 | // Green Laser Transistor -> Relay
113 | pinMode(GPIOB, GREEN_PIN, GPIO_OUTPUT);

114

115
116 | USART_TypeDef* USART = initUSART(USART_ID);

117
118 | // Print millis timer
119 | // PSC + 1 = 42000
120 | // 84MHz with a 42000 prescaler gives 0.5 ms resolution
121 | // Can count t0 32 seconds maximum
122 | TIM9->PSC = 41999;
123 | TIM9->CR1 |= (1 << 0); // Enable the counter
124 | TIM9->EGR |= (1 << 0); | // Generate an update event

125
126 | // Servo Micros Timer:
127 | // Goal, Count to 20,000, microsecond resolution
128 | // PSC + 1 = 84
129 | // 84MHz with a 84 prescaler gives microsecond resolution
130 | // Can count to 2^16 > 20,000
131 | TIM10->PSC = 83;
132 | TIM10->CR1 |= (1 << 0); // Enable the counter
133 | TIM10->EGR |= (1 << 0); | // Generate an update event

134
135 | // Beat Pin Millis Length Timer:
136 | // PSC + 1 = 42000
137 | // 84MHz with a 42000 prescaler gives 0.5 ms resolution
138 | // Can count t0 32 seconds maximum
139 | TIM11->PSC = 41999;
140 | TIM11->CR1 |= (1 << 0); // Enable the counter
141 | TIM11->EGR |= (1 << 0); | // Generate an update event

142

143
144 | TIM9->CNT = 0; | // Print
145 | TIM10->CNT = 0; // Servo Micros
146 | TIM11->CNT = 0; // BPM

147
148 | uint8_t prevBeatRead = 0; // boolean variable that tracks previous read value

149
150 | int beatIntervalMs = 10000;

151
152 | int patInd = 0;

153
154 | uint8_t patState = 0;

155
156 | digitalWrite(GPIOB, GREEN_PIN, 1);
157 | digitalWrite(GPIOA, RED_PIN, 1);

158
159 | while(1){

160
161 | // Pattern selection

162
163 | if(beatIntervalMs < 250){ //< 0.25sec, bpm > 240
164 | patInd = 0;
165 | } else if(beatIntervalMs < 500){ //< 0.5sec, bpm > 120
166 | patInd = 2;
167 | } else if(beatIntervalMs < 1000){ //< 1sec, bpm > 60
168 | patInd = 3;

169 | } else if (beatIntervalMs < 2000) { // < 2sec, 60 > bpm > 30
170 | patInd = 4;
171 | } else if (beatIntervalMs >= 2000){ // > 2sec, 30 > bpm
172 | patInd = 5;
173 | }

174
175 | // Writes Servo PWM signal out
176 | long curMicros = TIM10->CNT;
177 | long microsDes = pats[patInd][patState];
178 | if(curMicros < microsDes){
179 | digitalWrite(GPIOA, SERVO_PIN, 1);
180 | } else if(curMicros < CYCLE_MICROS){
181 | digitalWrite(GPIOA, SERVO_PIN, 0);
182 | } else {
183 | TIM10->CNT = 0;
184 | }

185
186 | uint8_t curBeatRead = digitalRead(GPIOA, BEAT_PIN);

187
188 | if (curBeatRead == 1 && prevBeatRead == 0){ // only on the rising edge
189 | beatIntervalMs = (TIM11->CNT)/2;

190
191 | digitalWrite(GPIOA, RED_PIN, pats[patInd][2]);
192 | digitalWrite(GPIOB, GREEN_PIN, pats[patInd][3]);

193
194 | // sprintf(text, "\n interval: %d | ind: %d | red: %d | green: %d\n",
,→ | beatIntervalMs, patInd, pats[patInd][2], pats[patInd][3]);
195 | // for (size_t j = 0; text[j]; j++) {
196 | // | sendChar(USART, text[j]);
197 | // }
198 | TIM11->CNT = 0;
199 | }
200 | prevBeatRead = curBeatRead;

201
202 | if(TIM9->CNT > 200){
203 | // sprintf(text, "\n%d | %d | %d\n", beatIntervalMs, patInd, patState);
204 | // for (size_t j = 0; text[j]; j++) {
205 | // | sendChar(USART, text[j]);
206 | // }
207 | TIM9->CNT = 0;
208 | }
209 | }
210 | }

REFERENCES

[1] G. Slade, “The fast fourier transform in hardware: A tutorial based on an FPGA implementation,” 03 2013.

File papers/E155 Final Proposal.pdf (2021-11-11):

E155 Final Project Proposal: Music Light Show Arya Goutam and Alec Vercruysse

Motivation:
Light shows are often used to enhance music but coordinating lighting with music is challenging to do on the fly, especially with a low-cost setup.

Goals:
Our overarching goal for this project is to design a system that automatically creates interesting lighting effects which are synchronized to a live audio input. Our subgoals include the following:
1. Read in Audio from a 3.5mm jack using an ADC.
2. Implement the FFT on the FPGA.
3. Implement an algorithm to produce lighting effects that are synchronized to some aspect of the music based on time and frequency information.
4. Communicate between FPGA and microcontroller.
5. Vary lighting using MCU based on FPGA input by selecting a pattern on a diffraction grating for a laser to shine through.

Design:
Digital acquisition is based on the simple and low-cost stereo audio PCM1808 ADC, which will communicate with our embedded system over an i2s interface. The FPGA will continuously perform windowed FFT functions, effectively computing the STFT sequentially. The output will be converted to a magnitude representation, and a digital filter will be applied to the output sequence (in time) that selects specific bins and an onset function. This onset function will be compared with a threshold value, and whenever a positive edge is encountered (e.g. the onset function rises above the threshold), the FPGA will increment a prescaler counter. When this prescaler is reset by overflow, the FPGA changes the selected pattern and reports this over a parallel bus to the MCU.

The MCU polls to find the pattern selection, and determines the angular range of the servo that corresponds to a laser shining through the specific pattern on the diffraction grating disk. It then drives a servo via PWM to within this angular range, slowly varying the angle to move the pattern. The laser circuitry and diffraction grating disk are taken from an existing laser light show product, and the diffraction grating disk is mounted on the servo.

Block Diagram:

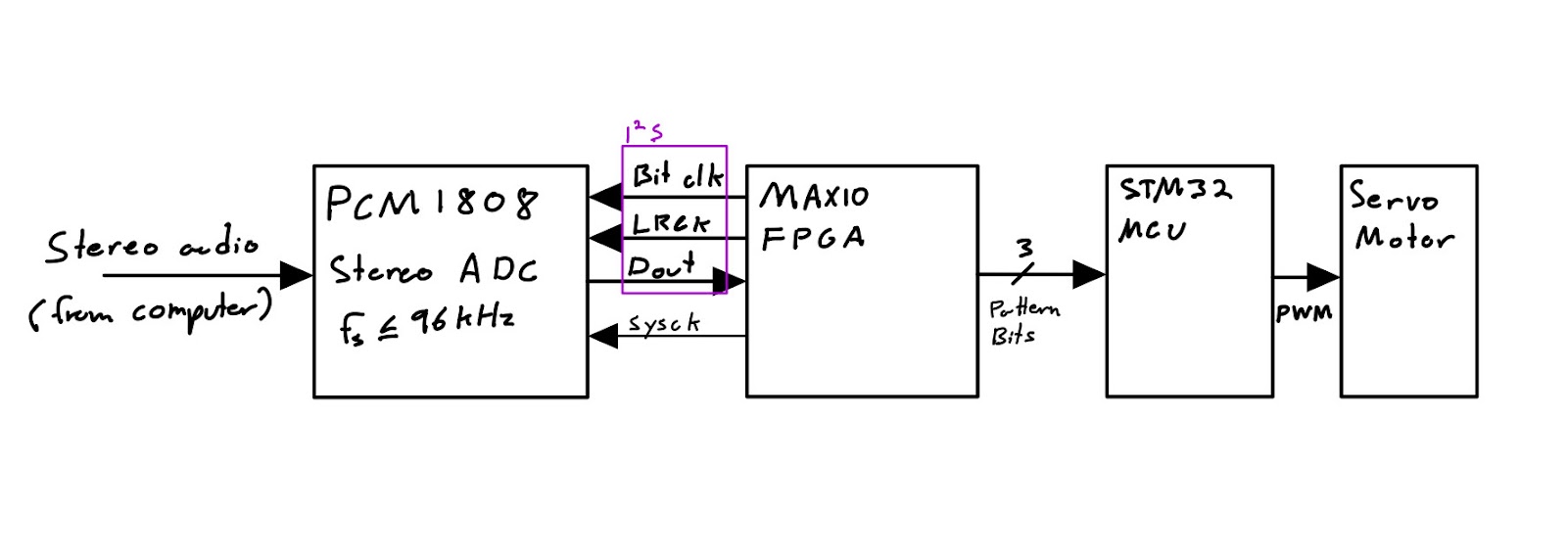
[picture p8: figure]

Figure 1: Hardware data-flow diagram. The PCM1808 ADC samples the audio and reports this to the MAX10 FPGA, which processes it and returns a “pattern selection” state to the MCU. The MCU determines the servo position given the pattern selection and drives the servo motor.

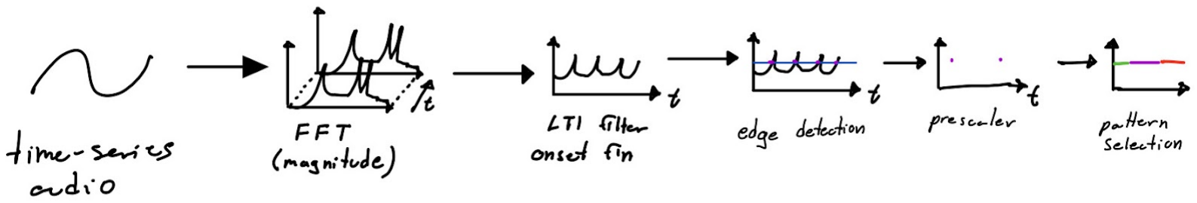
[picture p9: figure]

Figure 2: FPGA DSP data-flow diagram. An FFT is performed on the time-series audio, with magnitude output. An LTI filter selects relevant bins and calculates a novelty function. This is compared with a threshold to determine beat onsets, which, after a prescaler, turn into “pattern selection” state change impulses.

Budget:
Item | Cost
PCM1808 | $2.23
CAP CER 1UF 50V 0805 (x2) | $0.374
CAP CER 0.1UF 50V 0805 (x3) | $0.396
CAP CER 10UF 25V 080 (x3) | $1.26
CONN RCA JACK MONO 3.2MM (x2) | $4.36
CONN JACK STEREO 3.5MM SMD (x2) | $1.88
CONN HEADER VERT 40POS 2.54MM | $0.73
Digikey Shipping | $4.99
JLCPCB boards + shipping | $8.98
Laser + Diffraction Grating (https://www.ebay.com/itm/-/254626113887?mkevt=1&mkcid=16&mkrid=711-127632-2357-0) | $20.99
Hitec HS-311 Hobby Servo | $13.94 (already owned)
Total | $46.19

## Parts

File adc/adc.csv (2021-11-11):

Source: | /Users/alecvercruysse/Documents/hmc_classes/jr_fall/e155/final_project/adc/adc.sch
Date: | Tuesday, October 26, 2021 at 02:37:29 PM
Tool: | Eeschema (5.1.10-1-10_14)
Generator: | /private/var/folders/r3/43df3p2x51ldxyv9_n65s8c80000gn/T/AppTranslocation/6C9348F2-7580-4817-A3F4-A30D61205827/d/kicad.app/Contents/SharedSupport/plugins/bom_csv_grouped_by_value_with_fp.py
Component Count: | 15
Ref | Qnty | Value | Cmp name | Footprint | Description | Vendor
C1, C2, | 2 | 1uF | C | Capacitor_SMD:C_0805_2012Metric_Pad1.18x1.45mm_HandSolder | Unpolarized capacitor
C3, C5, C7, | 3 | 10uF | CP1_Small | Capacitor_SMD:C_0805_2012Metric_Pad1.18x1.45mm_HandSolder | Polarized capacitor, small US symbol
C4, C6, C8, | 3 | 0.1uF | C_Small | Capacitor_SMD:C_0805_2012Metric_Pad1.18x1.45mm_HandSolder | Unpolarized capacitor, small symbol
J1, J2, | 2 | RCJ-2123 | RCJ-2123 | custom_components:Coaxial-RCJ-2123
J3, J4, | 2 | SJ-3523-SMT-TR | AudioJack3 | Connector_Audio:Jack_3.5mm_CUI_SJ-3523-SMT_Horizontal | Audio Jack, 3 Poles (Stereo / TRS)
J5, | 1 | uMudd_40pin_conn | uMudd_40pin_conn | custom_components:S9175-ND | Generic connector, double row, 02x20, odd/even pin numbering scheme (row 1 odd numbers, row 2 even numbers), script generated (kicad-library-utils/schlib/autogen/connector/)
J8, | 1 | Servo Header | Conn_01x03_Male | Connector_PinHeader_2.54mm:PinHeader_1x03_P2.54mm_Vertical | Generic connector, single row, 01x03, script generated (kicad-library-utils/schlib/autogen/connector/)
U1, | 1 | PCM1808 | PCM1808 | Package_SO:TSSOP-14_4.4x5mm_P0.65mm

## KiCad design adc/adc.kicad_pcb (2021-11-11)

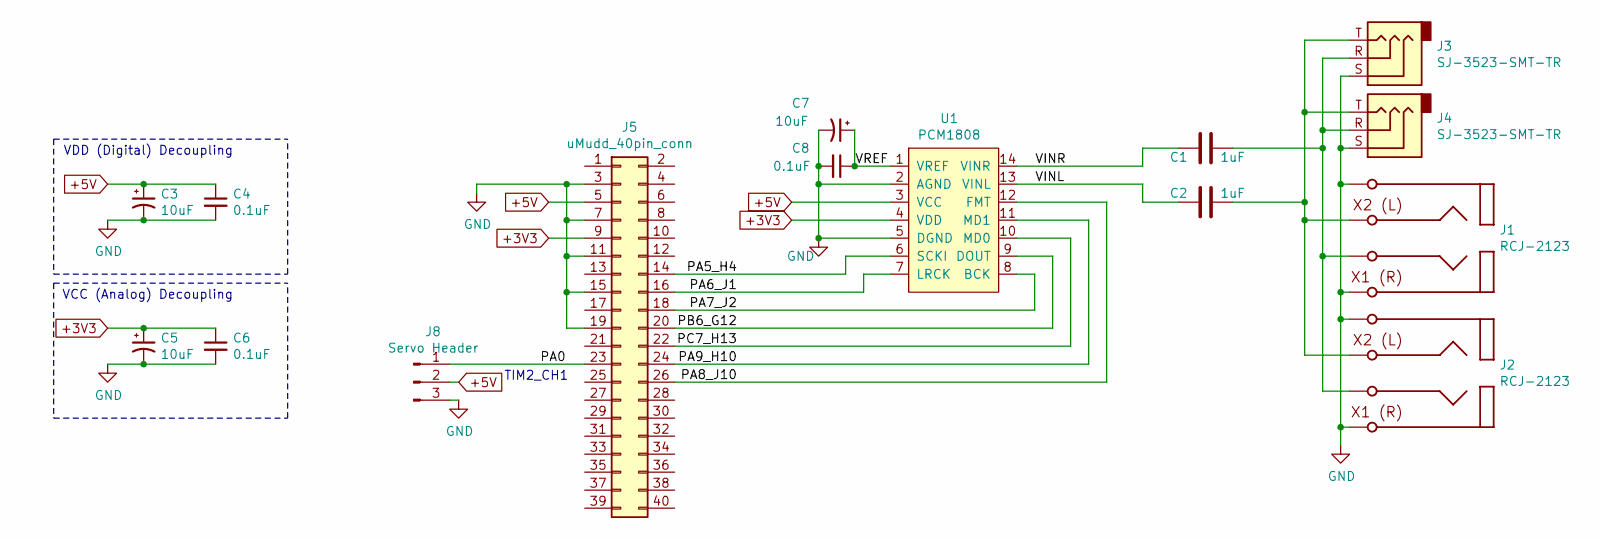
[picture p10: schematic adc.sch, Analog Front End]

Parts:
C1, C2: 1uF; C_0805_2012Metric_Pad1.18x1.45mm_HandSolder
C3, C5, C7: 10uF; C_0805_2012Metric_Pad1.18x1.45mm_HandSolder
C4, C6, C8: 0.1uF; C_0805_2012Metric_Pad1.18x1.45mm_HandSolder
J1, J2: RCJ-2123; Coaxial-RCJ-2123
J3, J4: SJ-3523-SMT-TR; Jack_3.5mm_CUI_SJ-3523-SMT_Horizontal
J5: uMudd_40pin_conn; S9175-ND
J8: Servo Header; PinHeader_1x03_P2.54mm_Vertical
U1: PCM1808; TSSOP-14_4.4x5mm_P0.65mm

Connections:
+3V3: C5.1, C6.1, J5.9, U1.4 (VDD)
+5V: C3.1, C4.1, J5.5, J8.2, U1.3 (VCC)
/PA0: J5.23, J8.1
/PA5_H4: J5.14, U1.6 (SCKI)
/PA6_J1: J5.16, U1.7 (LRCK)
/PA7_J2: J5.18, U1.8 (BCK)
/PA8_J10: J5.26, U1.12 (FMT)
/PA9_H10: J5.24, U1.11 (MD1)
/PB6_G12: J5.20, U1.9 (DOUT)
/PC7_H13: J5.22, U1.10 (MD0)
/VINL: C2.2, U1.13 (VINL)
/VINR: C1.2, U1.14 (VINR)
/VREF: C7.1, C8.1, U1.1 (VREF)
GND: C3.2, C4.2, C5.2, C6.2, C7.2, C8.2, J1.1, J1.3, J2.1, J2.3, J3.S, J4.S, J5.3, J5.7, J5.11, J5.15, J5.19, J8.3, U1.2 (AGND), U1.5 (DGND)
unnamed: C1.1, J1.2, J2.2, J3.R, J4.R
unnamed: C2.1, J1.4, J2.4, J3.T, J4.T

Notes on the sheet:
TIM2_CH1
VCC (Analog) Decoupling
VDD (Digital) Decoupling

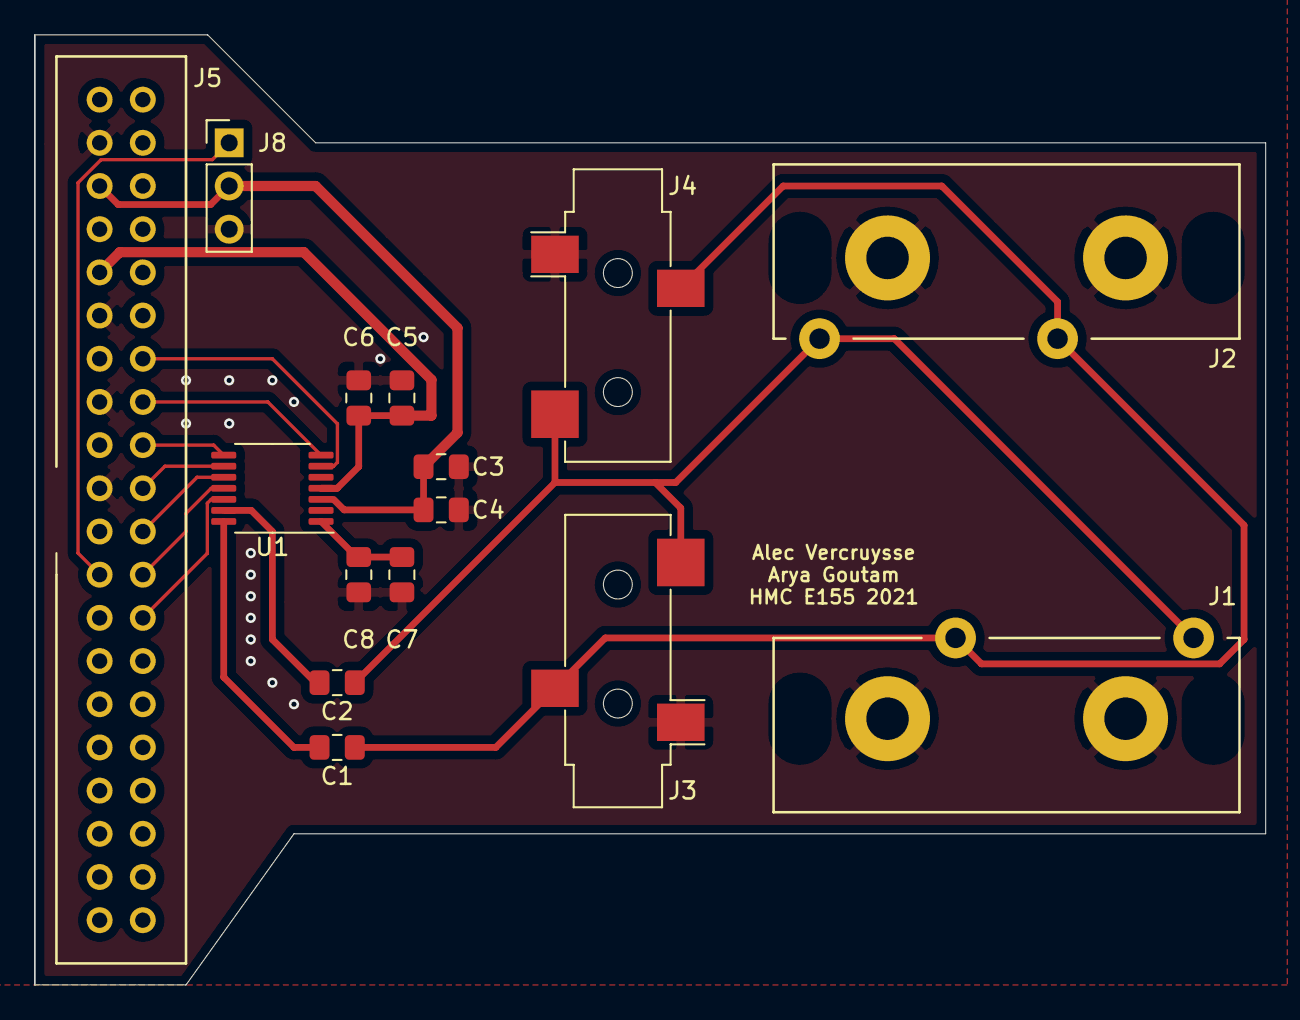
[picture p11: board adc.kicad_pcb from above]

Board: 4 copper layers, 72.4 x 55.9 mm, 15 parts (0 on the bottom side), 16 nets.

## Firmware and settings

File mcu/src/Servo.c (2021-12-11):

#include <stdio.h>
#include "STM32F401RE.h"

////////////////////////////////////////////////
// Constants
////////////////////////////////////////////////

#define SERVO_PIN    4 // GPIOA
#define BEAT_PIN     0 // GPIOA
#define GREEN_PIN    10 // GPIOB
#define RED_PIN      1 // GPIOA

#define USART_ID USART2_ID

#define MIN_MICROS 770
#define MAX_MICROS 2270
#define CYCLE_MICROS 20000

// Used for testing
const float usPerDeg = (MAX_MICROS - MIN_MICROS)/180;
// takes in an angle from 0-180, spits out microseconds to write to servo
long angleToMicros(float angle){
  return (long)(angle * usPerDeg) + MIN_MICROS;
}

// Servo Pattern points

// Red laser pattern locations
#define RPP0 770
#define RPP1 917
#define RPP2 1022
#define RPP3 1136
#define RPP4 1242
#define RPP5 1370
#define RPP6 1465
#define RPP7 1599
#define RPP8 1724
#define RPP9 1852
#define RPPA 1960
#define RPPB 2084
#define RPPC 2204
#define RPPD 2269

// Green laser pattern locations
#define GPP0 770  
#define GPP1 870
#define GPP2 966
#define GPP3 1091
#define GPP4 1208
#define GPP5 1328
#define GPP6 1442
#define GPP7 1532
#define GPP8 1664
#define GPP9 1792
#define GPPA 1862
#define GPPB 1978
#define GPPC 2134
#define GPPD 2269   

//Pattern set 1

// start, end, red, green
//  int pats[6][4] = {
//                        {GPP0,  GPP1, 1, 1},
//                        {RPP0,  RPP1, 0, 1},
//                        {GPP2, GPP3,  1, 1},
//                        {RPP3, RPP4,  1, 0},
//                        {RPP5, RPP6,  1, 0},
//                        {RPP7, RPP8,  1, 0} //1328, 1442
//                        };

// Pattern set 2

int pats[6][4] = {
                  {GPPC,  GPPD, 1, 1},
                  {GPPA,  GPPB, 1, 1},
                  {GPP8, GPP9,  0, 1},
                  {RPP6, RPP7,  1, 0},
                  {RPP4, RPP5,  1, 0},
                  {RPP2, RPP3,  1, 0}
                  };

// used for printing
char text[50];

int main(void) {
  // Configure flash latency and set clock to run at 84 MHz
  configureFlash();

  /* Configure APB prescalers
      1. Set APB2 (high-speed bus) prescaler to no division
      2. Set APB1 (low-speed bus) to divide by 2.
  */
  RCC->CFGR.PPRE2 = 0b000;
  RCC->CFGR.PPRE1 = 0b100;

  configureClock();

  // Enable GPIOA clock
  RCC->APB2ENR |= (1 << 16); //Enable TIM10
  RCC->APB2ENR |= (1 << 17); //Enable TIM10
  RCC->APB2ENR |= (1 << 18); //Enable TIM11
  RCC->AHB1ENR.GPIOAEN = 1; // Enable GPIOA Clock
  RCC->AHB1ENR.GPIOBEN = 1; // Enable GPIOB Clock

  // Servo Pin
  pinMode(GPIOA, SERVO_PIN, GPIO_OUTPUT);
  // Beat Pin from FPGA
  pinMode(GPIOA, BEAT_PIN, GPIO_INPUT);
  // Red Laser Transistor -> Relay
  pinMode(GPIOA, RED_PIN, GPIO_OUTPUT);
  // Green Laser Transistor -> Relay
  pinMode(GPIOB, GREEN_PIN, GPIO_OUTPUT);


  USART_TypeDef* USART = initUSART(USART_ID);

  // Print millis timer
  // PSC + 1 = 42000
  // 84MHz with a 42000 prescaler gives 0.5 ms resolution
  // Can count t0 32 seconds maximum
  TIM9->PSC = 41999;
  TIM9->CR1 |= (1 << 0); // Enable the counter
  TIM9->EGR |= (1 << 0);  // Generate an update event

  // Servo Micros Timer:
  // Goal, Count to 20,000, microsecond resolution
  // PSC + 1 = 84
  // 84MHz with a 84 prescaler gives microsecond resolution
  // Can count to 2^16 > 20,000
  TIM10->PSC = 83;
  TIM10->CR1 |= (1 << 0); // Enable the counter
  TIM10->EGR |= (1 << 0);  // Generate an update event

  // Beat Pin Millis Length Timer:
  // PSC + 1 = 42000
  // 84MHz with a 42000 prescaler gives 0.5 ms resolution
  // Can count t0 32 seconds maximum
  TIM11->PSC = 41999;
  TIM11->CR1 |= (1 << 0); // Enable the counter
  TIM11->EGR |= (1 << 0);  // Generate an update event


  TIM9->CNT = 0;  // Print
  TIM10->CNT = 0; // Servo Micros
  TIM11->CNT = 0; // BPM

  uint8_t prevBeatRead = 0; // boolean variable that tracks previous read value
  int beatIntervalMs = 10000; // keeps track of time since last beat in ms?
  int patInd = 0;             // pattern index pats[idx][0:start, 1:end, 2:red, 3:green]
  uint8_t patState = 0;       // 0 or 1 (e.g. start or end state)

  digitalWrite(GPIOB, GREEN_PIN, 1);
  digitalWrite(GPIOA, RED_PIN, 1);

  while(1){

    // Pattern selection
    
    if(beatIntervalMs < 250){ //< 0.25sec, bpm > 240
      patInd = 0;
    } else if(beatIntervalMs < 500){ //< 0.5sec, bpm > 120
      patInd = 2;
    } else if(beatIntervalMs < 1000){ //< 1sec, bpm > 60
      patInd = 3;
    } else if (beatIntervalMs < 2000) { // < 2sec, 60 > bpm > 30 
      patInd = 4;
    } else if (beatIntervalMs >= 2000){ // > 2sec, 30 > bpm
      patInd = 5;
    }

    // Writes Servo PWM signal out
    long curMicros = TIM10->CNT;
    long microsDes = pats[patInd][patState];
    if(curMicros < microsDes){
      digitalWrite(GPIOA, SERVO_PIN, 1);
    } else if(curMicros < CYCLE_MICROS){
      digitalWrite(GPIOA, SERVO_PIN, 0);
    } else {
      TIM10->CNT = 0;
    }
        
    uint8_t curBeatRead = digitalRead(GPIOA, BEAT_PIN);
    if (curBeatRead == 1 && prevBeatRead == 0){ // only on the rising edge
      beatIntervalMs = (TIM11->CNT)/2;
      patState ^= 1;
      digitalWrite(GPIOA, RED_PIN, pats[patInd][2]);
      digitalWrite(GPIOB, GREEN_PIN, pats[patInd][3]);

      // sprintf(text, "\n interval: %d | ind: %d | red: %d | green: %d\n", beatIntervalMs, patInd, pats[patInd][2], pats[patInd][3]);
      // for (size_t j = 0; text[j]; j++) {
      //     sendChar(USART, text[j]);
      // }
      TIM11->CNT = 0;
    }
    prevBeatRead = curBeatRead;

    if(TIM9->CNT > 200){
        // sprintf(text, "\n%d  %d  %d\n", beatIntervalMs, patInd, patState);
        // for (size_t j = 0; text[j]; j++) {
        //     sendChar(USART, text[j]);
        // }
        TIM9->CNT = 0;
    }
  }
}

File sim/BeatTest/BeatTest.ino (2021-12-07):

#define OUT_PIN 5

void setup() {
  pinMode(OUT_PIN, OUTPUT);
  digitalWrite(OUT_PIN, LOW);
  Serial.begin(115200);
}

void loop() {
  for(int i = 0; i < 10; i++){
    digitalWrite(OUT_PIN, HIGH);
    delayMicroseconds(170);
    digitalWrite(OUT_PIN, LOW);
    delayMicroseconds(830);
    delay(499);
    Serial.print("fast");
    Serial.println(i);
  }

  for(int i = 0; i < 5; i++){
    digitalWrite(OUT_PIN, HIGH);
    delayMicroseconds(170);
    digitalWrite(OUT_PIN, LOW);
    delayMicroseconds(830);
    delay(1100);
    Serial.print("mid");
    Serial.println(i);
  }

  for(int i = 0; i < 5; i++){
    digitalWrite(OUT_PIN, HIGH);
    delayMicroseconds(170);
    digitalWrite(OUT_PIN, LOW);
    delayMicroseconds(830);
    delay(2200);
    Serial.print("slow");
    Serial.println(i);
  }
}

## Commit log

2021-11-20 switch to 32-point FFT
2021-11-21 pin planning
2021-11-30 i2s -> fft glue logic, verified only one cycle
2021-12-06 get working spectrum output via SPI/mcu -> uart/PC
2021-12-07 adding servo code
2021-12-07 adding c++ implementation of fft used to verify verilog, as well as code that runs on Arduino and outputs a simulated beat at varying frequencies to test pattern creation.
2021-12-08 working Servo.c
2021-12-11 bugfix: pattern state not toggling on beat in.
    - remove main.c, since it is not relevant. This is present in (and
    only relevant to) the fft_display branch.
    [Servo.c]
2021-12-11 update LEDs only on beat (as previously)
